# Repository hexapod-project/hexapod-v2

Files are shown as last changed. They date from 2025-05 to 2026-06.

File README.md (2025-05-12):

# Hexapod v2

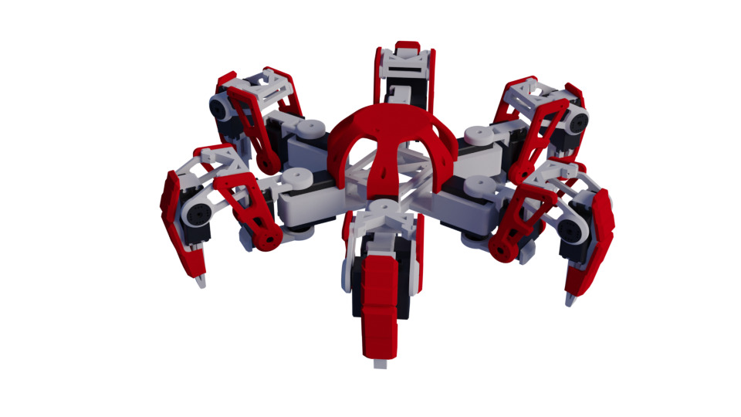
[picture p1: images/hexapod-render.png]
Hexapod v2


This is a hexapod robot that was built based on the previous version [(Hexapod v1)](https://github.com/hexapod-project/hexapod-v1) but with simpler basic features, more efficient inverse kinematics algorithm, and better structured code. This is a base that will be used for more advanced features in the future.

## Hardwares
- Microcontroller: Esp32
- Servo controller: PCA9685 (2 boards, 3 legs (9 servos) per board)
- Servos: 18 x DSPower Servo - S020A (30KG servo) (Or any other servos that has the same dimension, mounting points and max. torque)
- Batteries: 1 x 6v 2400mAh Ni-MH (for powering the microcontroller), 1 x 7.4v 2600mAh Li-ion/Ni-Mh (for powering the servos)
- Esp32 Expansion Shield (Optional)
- A switch (Optional) - Eg. Rocker switch or toggle switch

## Libraries

- Arduino Esp32
- Adafruit_PWMServoDriver
- PlatformIO

## Circuit Diagram

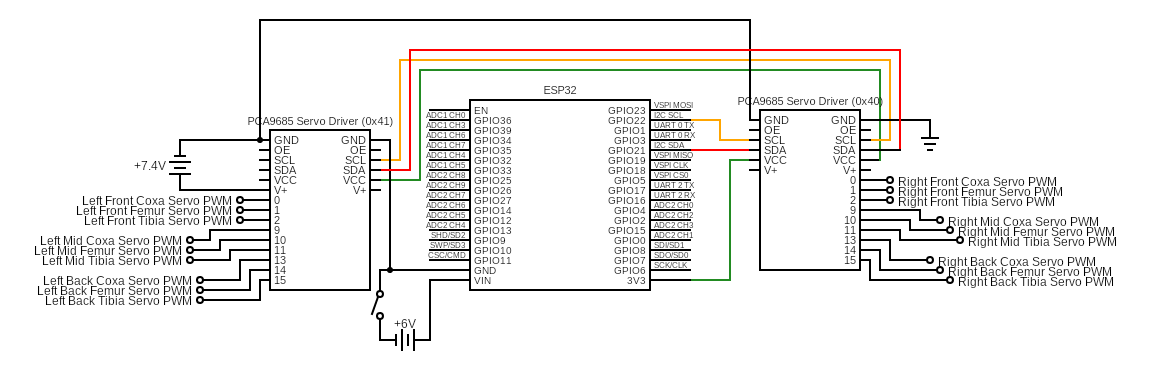
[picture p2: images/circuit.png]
Circuit Diagram


## Assembly

- All parts can be found in the [stl](/stl) folder
- The parts can be 3D printed using PLA with 0.4 nozzle.

##### Body

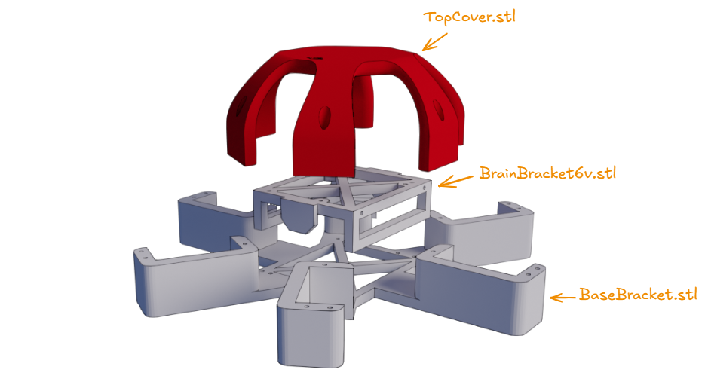
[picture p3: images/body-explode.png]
Body Explode View


- Use M3 x 20cm screws to attach the [TopCover.stl](/stl/TopCover.stl) to the [BaseBracket.stl](/stl/BaseBracket.stl)
- Use M3 screws to attach the ESP32 and PCA9685 Servo Drivers to the [BaseBracket.stl](/stl/BaseBracket.stl)

#### Servo

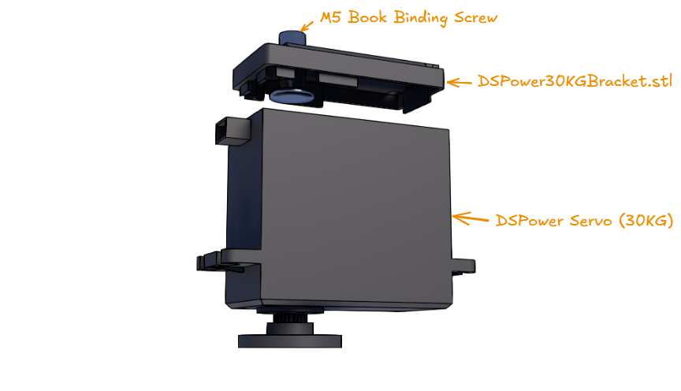
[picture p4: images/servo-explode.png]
Servo Explode View


- Remove the bottom cover of the servo and replace it with the [DSPower30KGBracket.stl](/stl/DSPower30KGBracket.stl) and insert a M5 Book Binding Screw to the hole as a pivot for the joints.

#### Leg

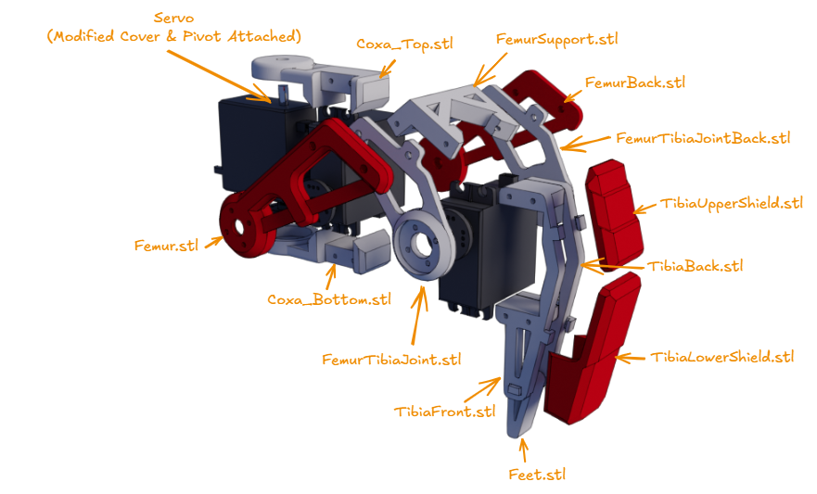
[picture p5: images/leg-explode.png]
Leg Explode View


- Assemble the leg parts according to the figure above.
- Use the screws provided by the servos to attach the parts to the servo.
- The legs are designed for the right legs but the parts can be flipped to be used for the left legs.

#### Body and Leg Attachment

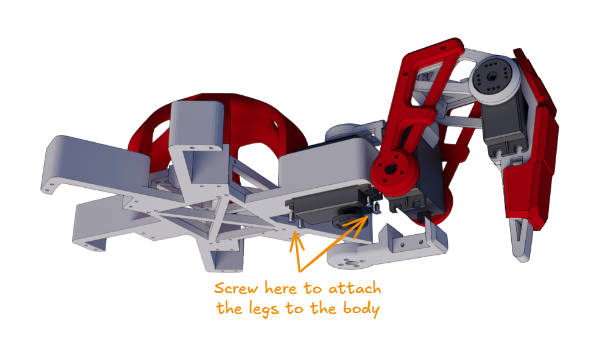
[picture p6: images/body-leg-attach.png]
Body and Leg Attachment


- Remove the CoxaBottom part and attach the leg to the body using the screws provided by the servos.

#### Final Assembly

Final Assembly

## Future Improvements

- Add Inertial Measurement Unit (IMU) for balancing
- Add LIDAR for obstacle detection
- Add GPS for position tracking
- Add path finding algorithm
- Migrate to Raspberry Pi for more processing power

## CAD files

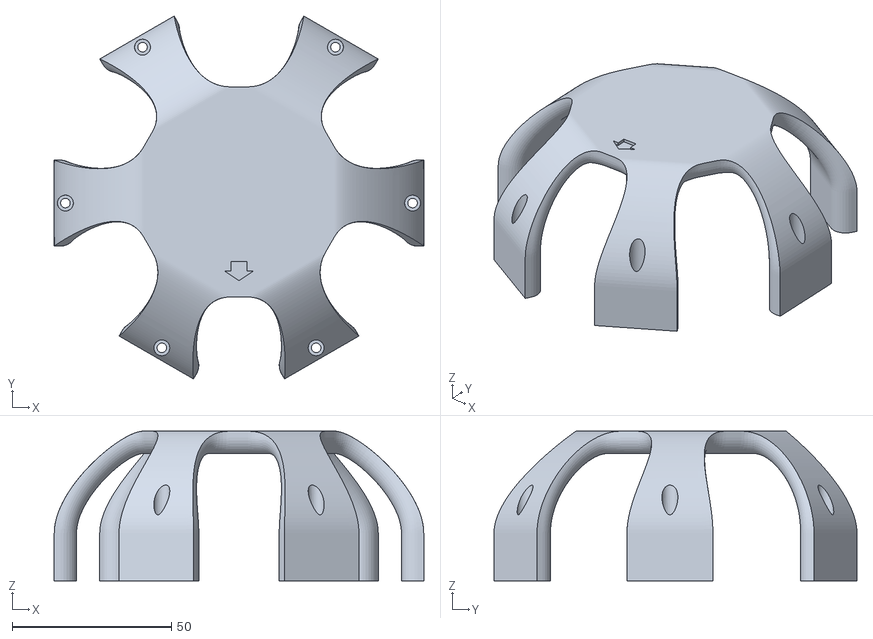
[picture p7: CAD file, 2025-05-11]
stl/TopCover.stl
116.0 x 114.0 x 47.0

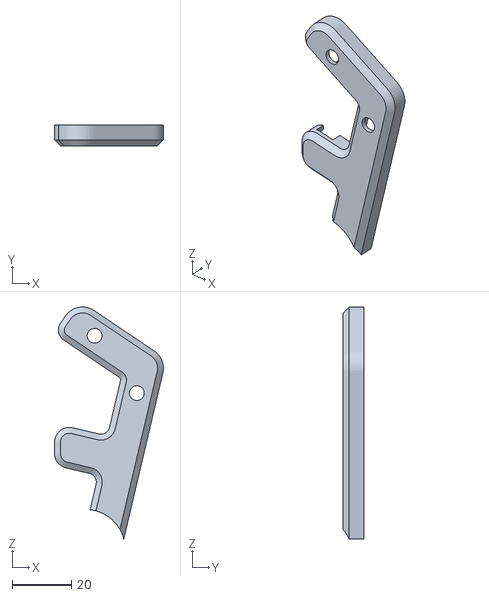
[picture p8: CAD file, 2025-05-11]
stl/FemurShield.stl
36.8 x 7.00 x 78.4

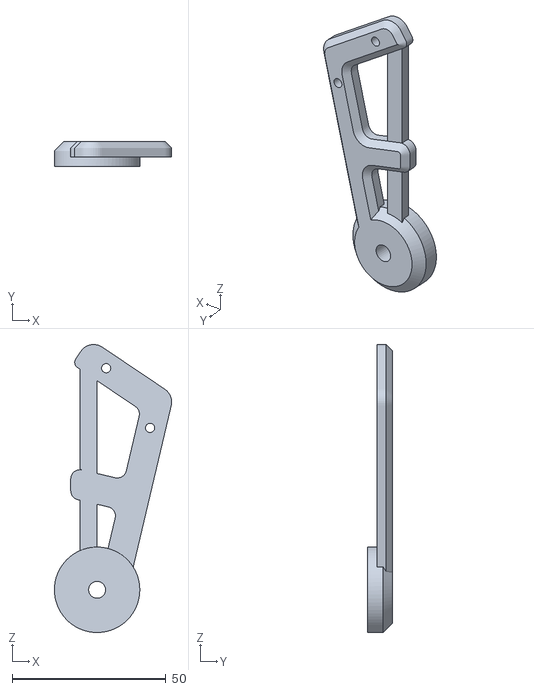
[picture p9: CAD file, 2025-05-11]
stl/FemurBack.stl
38.1 x 8.00 x 93.6

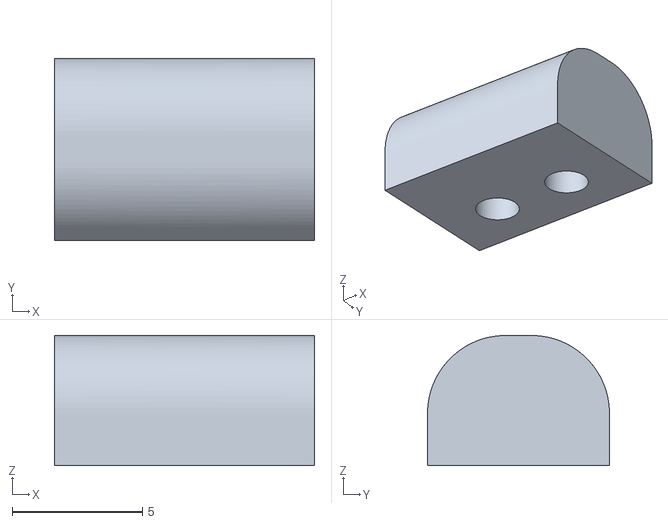
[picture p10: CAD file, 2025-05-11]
stl/BaterryBracke7.4v_Notch.stl
10.0 x 7.00 x 5.00

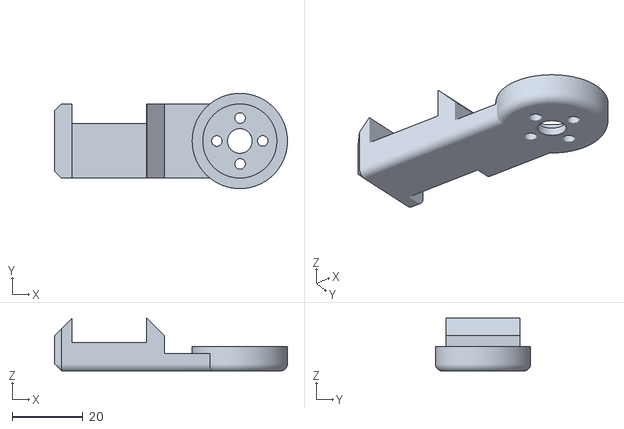
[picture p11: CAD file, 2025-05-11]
stl/Coxa_Bottom.stl
66.0 x 27.0 x 15.0

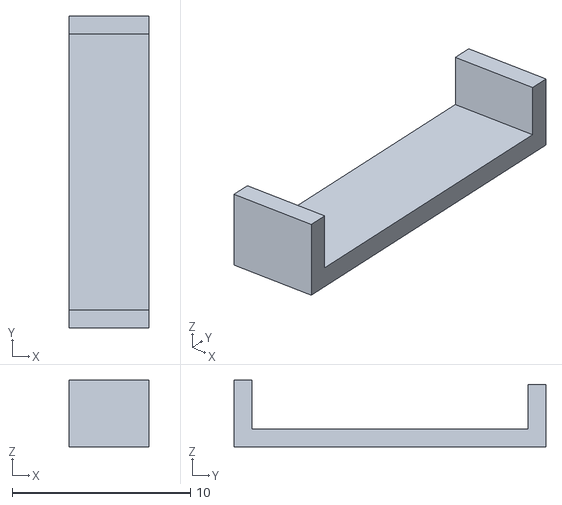
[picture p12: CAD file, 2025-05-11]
stl/DowelHolder.stl
4.50 x 17.5 x 3.75

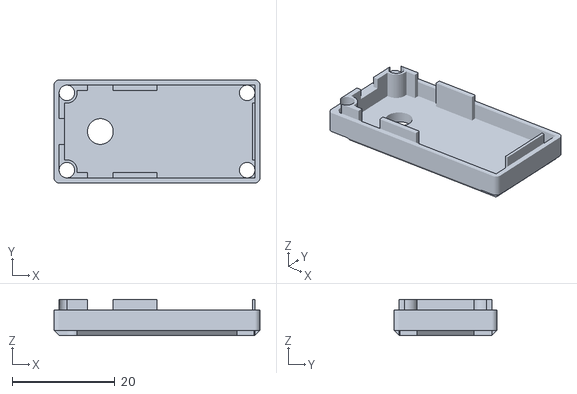
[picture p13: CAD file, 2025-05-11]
stl/DSPower30KGBracket.stl
40.0 x 20.0 x 7.00

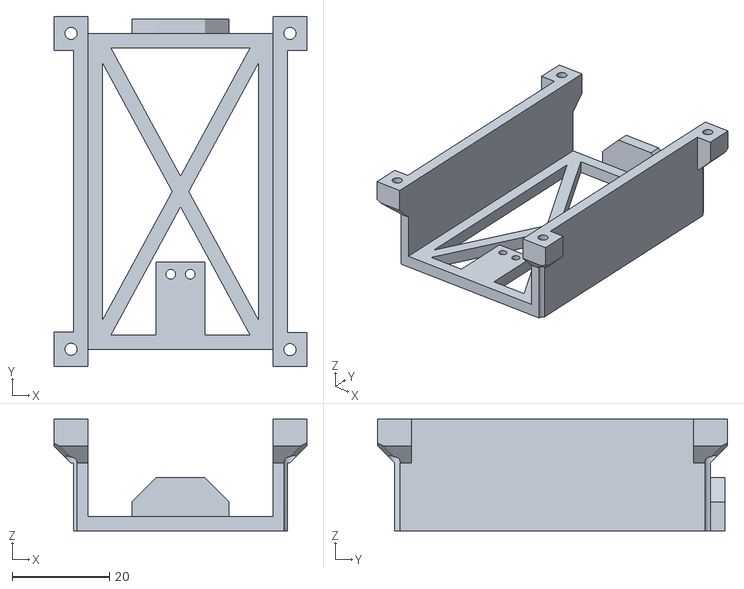
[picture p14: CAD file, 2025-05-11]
stl/BaterryBracke7.4v.stl
52.0 x 72.0 x 23.0

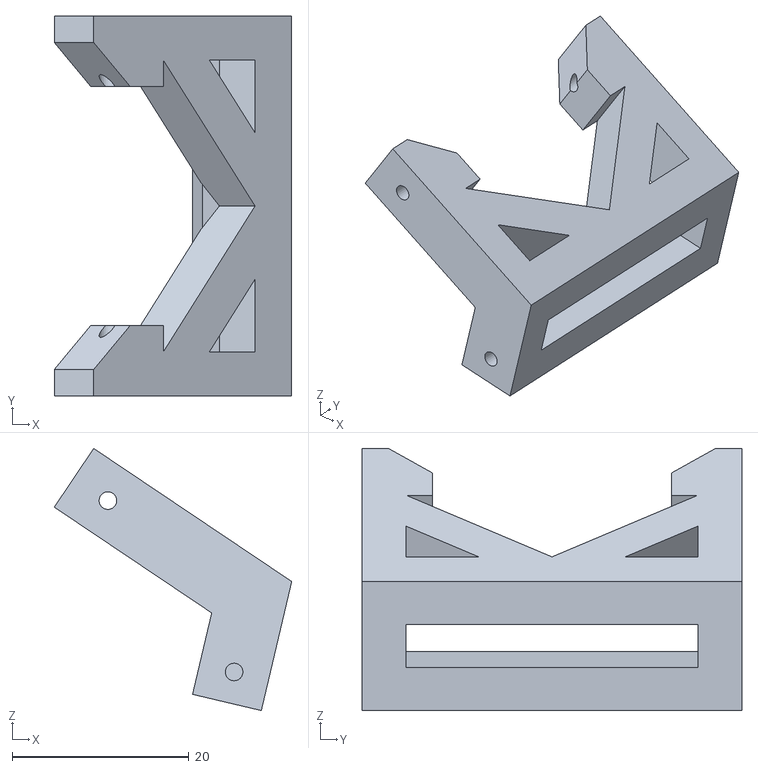
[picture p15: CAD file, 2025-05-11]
stl/FemurSupport.stl
26.9 x 43.0 x 29.7

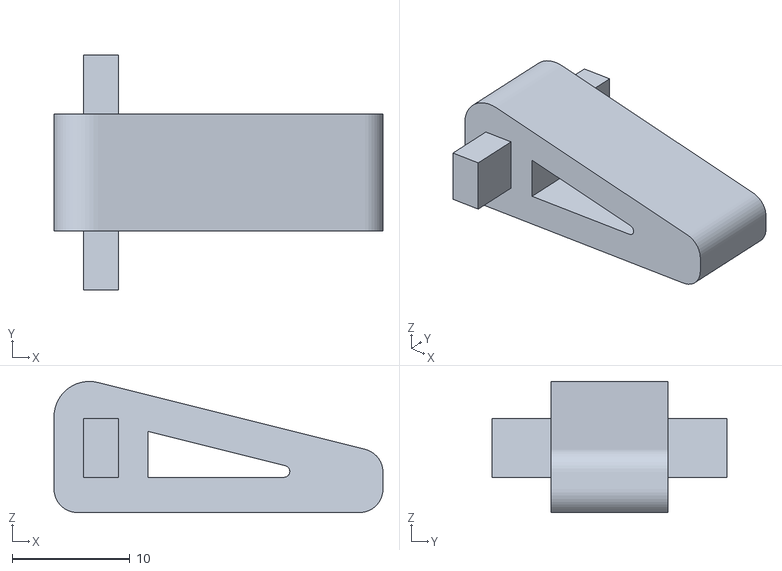
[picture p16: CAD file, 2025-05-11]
stl/Feet.stl
28.0 x 20.0 x 11.2

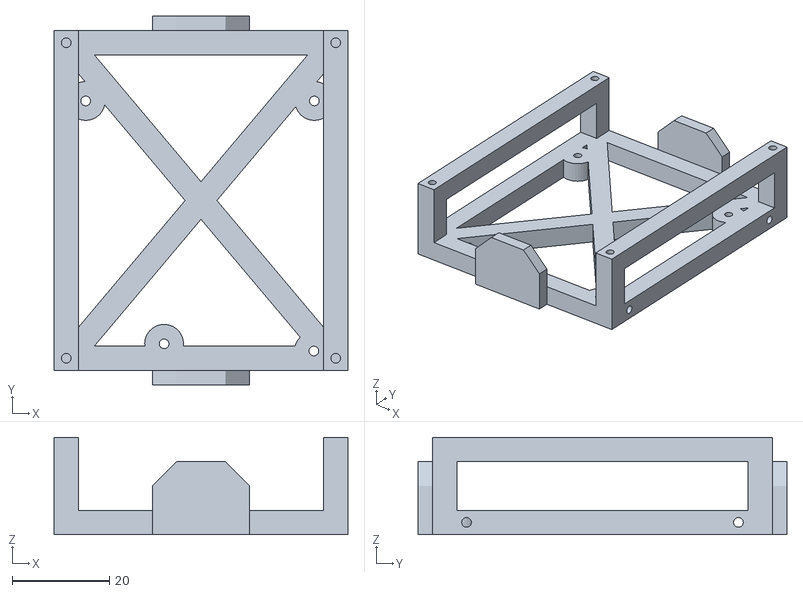
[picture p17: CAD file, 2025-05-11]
stl/BrainBracket6v.stl
60.5 x 76.0 x 20.0

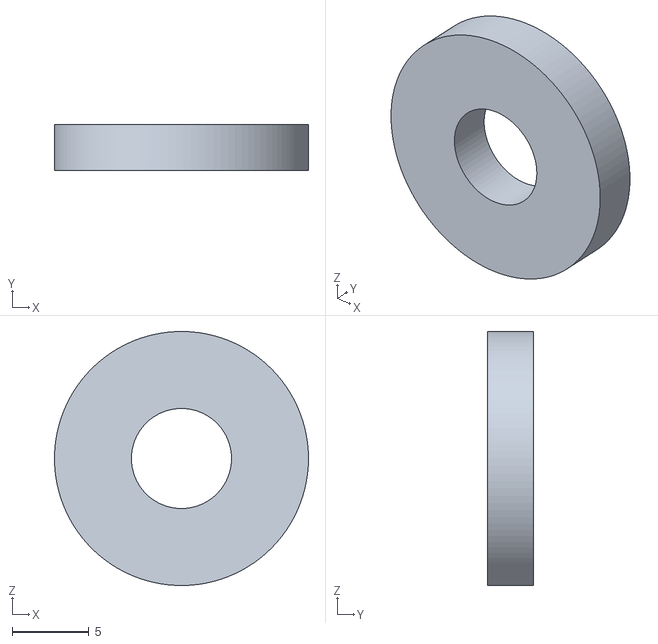
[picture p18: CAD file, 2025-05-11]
stl/Spacer_3mm.stl
16.5 x 3.00 x 16.5

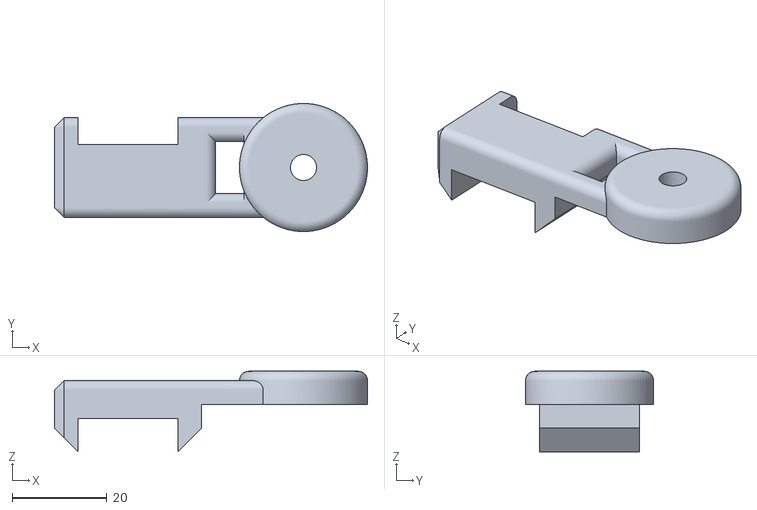
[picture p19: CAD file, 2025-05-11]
stl/Coxa_Top.stl
66.0 x 27.0 x 17.0

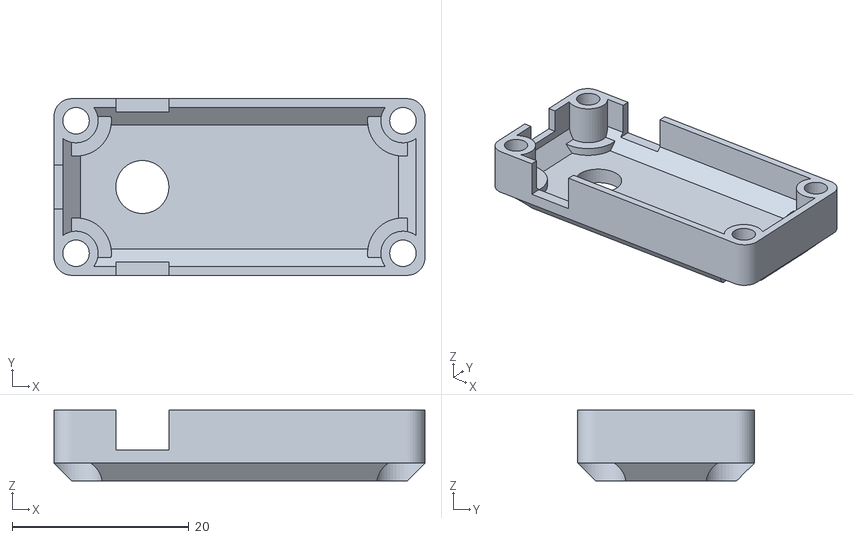
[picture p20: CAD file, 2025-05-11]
stl/ServoBracket.stl
42.0 x 20.0 x 8.00

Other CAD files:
stl/TibiaFront.stl
stl/Spacer_1mm.stl
stl/TibiaUpperShield.stl
stl/MagnetBracket_Male.stl
stl/BaseBracket.stl
stl/BaterryBracket7.4v_Notch2.stl
stl/BatteryBracket.stl
stl/BatteryBracket7.4v.stl
stl/BrainBracket.stl
stl/Femur.stl
stl/FemurTibiaJoint.stl
stl/FemurTibiaJointBack.stl
stl/MagnetBracket_Female.stl
stl/ServoBracket-DowelHolder.stl
stl/SwitchHolder.stl
stl/TibiaBack.stl
stl/TibiaLowerShield.stl
stl/Washer_2mmHole.stl

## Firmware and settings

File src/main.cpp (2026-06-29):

#include <string>
#include <Arduino.h>
#include <Preferences.h>

#include "Hexapod.h"
#include "Configuration.h"
#include "HexapodBLE.h"
#include "Constants.h"
#include "Calibrator.h"
#include "Utils.h"
#include "DisplayManager.h"
#include "MenuController.h"
#include "StateMachine.h"

bool isConnected = false;

int bluetoothMessage;
DisplayManager displayManager = DisplayManager();
Hexapod hexapod = Hexapod();
HexapodBLE hexapodBLE = HexapodBLE();
Calibrator calibrator = Calibrator(&hexapod);
StateMachine stateMachine = StateMachine();
MenuController menuController = MenuController(&displayManager, &calibrator, &stateMachine);

class HexapodBLEServerCallbacks : public BLEServerCallbacks
{
  void onConnect(BLEServer *server)
  {
    Serial.println("Bluetooh Connected");
    server->getAdvertising()->stop();
  }

  void onDisconnect(BLEServer *server)
  {
    Serial.println("Bluetooth Disconnected");
    server->startAdvertising();
    hexapod.stop();
  }
};

class MoveCharacteristicCallbacks : public BLECharacteristicCallbacks
{
  void onWrite(BLECharacteristic *characteristic)
  {
    std::string moveData = characteristic->getValue();
    int walkDirection = std::stoi(moveData);

    Serial.println(walkDirection);

    if (walkDirection >= 0)
    {
      hexapod.startWalk(walkDirection);
      stateMachine.moving(walkDirection);
    }
    else
    {
      hexapod.stop();
      stateMachine.idle();
    }
  }
};

class RotateCharacteristicCallbacks : public BLECharacteristicCallbacks
{
  void onWrite(BLECharacteristic *characteristic)
  {
    std::string moveData = characteristic->getValue();
    RotateDirection rotateDirection = static_cast<RotateDirection>(std::stoi(moveData));

    switch (rotateDirection)
    {
    case RotateDirection::ROTATE_LEFT:
    case RotateDirection::ROTATE_RIGHT:
      hexapod.startRotate(rotateDirection);
      break;
    default:
      hexapod.stop();
    }
  }
};

class RollPitchCharacteristicCallbacks : public BLECharacteristicCallbacks
{
  void onWrite(BLECharacteristic *characteristic)
  {
    std::string rollPitchData = characteristic->getValue();
    int rollPitchAngle = std::stoi(rollPitchData);

    if (rollPitchAngle >= 0)
    {
      hexapod.rollAndPitch(rollPitchAngle);
      if (rollPitchAngle >= 80 && rollPitchAngle <= 100)
      {
        // displayManager.displayAngryAnim();
      }
      else if (rollPitchAngle >= 260 && rollPitchAngle < 280)
      {
        // displayManager.displayHappyAnim();
      }
    }
    else
    {
      hexapod.stand();
    }
  }
};

class PWMPulseCharacteristicCallbacks : public BLECharacteristicCallbacks
{
  void onRead(BLECharacteristic *characteristic)
  {
    uint8_t *calibrationSettings = calibrator.getCalibrationSettings();
    std::string value = byteArrayToString(calibrationSettings, SERVO_COUNT * sizeof(u_int16_t));

    characteristic->setValue(value);
  }

  void onWrite(BLECharacteristic *characteristic)
  {
    std::string pwmPulseData = characteristic->getValue();

    uint8_t servoIndex = pwmPulseData[0];
    uint16_t pulse = (pwmPulseData[1] << 8) | pwmPulseData[2];

    calibrator.setPWMPulse(servoIndex, pulse);
  }
};

class MoveServoCharacteristicCallbacks : public BLECharacteristicCallbacks
{
  void onWrite(BLECharacteristic *characteristic)
  {
    std::string pwmPulseData = characteristic->getValue();

    uint8_t servoIndex = pwmPulseData[0];
    short angle = pwmPulseData[1] + SERVO_ANGLES_MIN;

    calibrator.testServoAngle(servoIndex, angle);
  }
};

class HexapodModeCharacteristicCallbacks : public BLECharacteristicCallbacks
{
  void onRead(BLECharacteristic *characteristic)
  {
    HexapodMode mode = hexapod.getMode();

    characteristic->setValue(std::to_string(mode));
  }

  void onWrite(BLECharacteristic *characteristic)
  {
    std::string modeData = characteristic->getValue();
    HexapodMode mode = static_cast<HexapodMode>(std::stoi(modeData));

    hexapod.switchMode(mode);
  }
};

class HexapodRestCharacteristicCallbacks : public BLECharacteristicCallbacks
{
  void onRead(BLECharacteristic *characteristic)
  {
    bool isSleep = stateMachine.getState() == STATE_SLEEP;

    characteristic->setValue(std::to_string(isSleep));
  }

  void onWrite(BLECharacteristic *characteristic)
  {
    std::string isSleep = characteristic->getValue();

    if (isSleep == "1")
    {
      stateMachine.sleep();
    }
    else
    {
      stateMachine.idle();
    }
  }
};

void setup()
{
  Serial.begin(115200);

  hexapodBLE.initBLE(new HexapodBLEServerCallbacks(),
                     new MoveCharacteristicCallbacks(),
                     new RotateCharacteristicCallbacks(),
                     new RollPitchCharacteristicCallbacks(),
                     new PWMPulseCharacteristicCallbacks(),
                     new MoveServoCharacteristicCallbacks(),
                     new HexapodModeCharacteristicCallbacks(),
                     new HexapodRestCharacteristicCallbacks());

  calibrator.init();
  displayManager.init();
  displayManager.startLoading();

  hexapod.init();

  displayManager.stopLoading();
  menuController.init();

  stateMachine.init();
  stateMachine.idle();
}

void loop()
{
  menuController.loop();
  displayManager.loop();
  stateMachine.loop();
}

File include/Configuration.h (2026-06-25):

#pragma once

#include <map>
#include "Servo.h"
#include "Leg.h"
#include "Vec3.h"
#include <Adafruit_PWMServoDriver.h>

// 0 = Hexapod, 1 = Servo Calibration, 2 = Servo Tests
#define MODE 0
#define DEBUG_MODE_LEGS false
#define SERIAL_CONTROL_MODE false

// Servo Constants
#define SERVO_ANGLES_MIN -75
#define SERVO_ANGLES_MAX 75
#define PWM_FREQ 60

#define SCREEN_WIDTH 128  // OLED display width, in pixels
#define SCREEN_HEIGHT 64  // OLED display height, in pixels
#define HALF_SCREEN_WIDTH SCREEN_WIDTH/2
#define HALF_SCREEN_HEIGHT SCREEN_HEIGHT/2
#define OLED_RESET -1    // Reset pin # (or -1 if sharing Arduino reset pin)
#define OLED_I2C_ADDRESS 0x3C

extern Adafruit_PWMServoDriver *servoDriverRight;
extern Adafruit_PWMServoDriver *servoDriverLeft;

extern std::map<int, Servo *> SERVOS;

// Leg Constants
// Lengths in mm
#define COXA_DISTANCE_FROM_CENTER 90
#define FEMUR_TO_COXA_DISTANCE 40
#define FEMUR_LENGTH 70
#define TIBIA_LENGTH 90

extern std::map<int, Leg *> LEGS;

// Body Positions
#define BODY_OFFSET_Z 10

// Feet Properties
#define REST_HEIGHT 0
#define STAND_HEIGHT 50
#define FEET_DISTANCE_FROM_CENTER_REST 180
#define FEET_DISTANCE_FROM_CENTER_STANDING 190

extern std::map<int, Vec3 *> FEET_POSITIONS_STANDING;
extern std::map<int, Vec3 *> FEET_POSITIONS_REST;

// Step Properties
#define STEP_FRAMERATE 24 // How often to update the gaits
#define STEP_DISTANCE 150
#define STEP_HEIGHT 80
#define STEP_DURATION 0.3 // in seconds +500ms(i2c delay)

// Roll Pitch Properties
#define ROLL_ANGLE 20
#define PITCH_ANGLE 20

// Rotate Properties
#define ROTATE_ANGLE_PER_STEP 20

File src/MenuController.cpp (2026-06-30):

#include "MenuController.h"
#include "Constants.h"
#include <Arduino.h>

std::map<MenuScreen, String> MENU_LABELS = {
    {MENU_MAIN, "Main Menu"},
    {MENU_MOOD, "Change Mood"},
    {MENU_CALIBRATE, "Calibrate"},
    {MENU_SLEEP, "Sleep"},
    {MENU_OFF, "Power Off"},
    {MENU_RESET, "Reset to Default"},
    {MENU_RESET_CONFIRMATION, "Reset to Default"},
    {MENU_EXIT, "Exit"},
    {MENU_BACK, "Back"},

    {MENU_MOOD_NEUTRAL, "Neutral"},
    {MENU_MOOD_HAPPY, "Happy"},
    {MENU_MOOD_SAD, "Sad"},
    {MENU_MOOD_ANGRY, "Angry"},
    {MENU_MOOD_TIRED, "Tired"},
    {MENU_MOOD_SLEEP, "Sleep"},

    {MENU_CALIBRATE_LF_COXA, "Left Front Coxa"},
    {MENU_CALIBRATE_LM_COXA, "Left Mid Coxa"},
    {MENU_CALIBRATE_LB_COXA, "Left Back Coxa"},
    {MENU_CALIBRATE_RF_COXA, "Right Front Coxa"},
    {MENU_CALIBRATE_RM_COXA, "Right Mid Coxa"},
    {MENU_CALIBRATE_RB_COXA, "Right Back Coxa"},

    {MENU_CALIBRATE_LF_FEMUR, "Left Front Femur"},
    {MENU_CALIBRATE_LM_FEMUR, "Left Mid Femur"},
    {MENU_CALIBRATE_LB_FEMUR, "Left Back Femur"},
    {MENU_CALIBRATE_RF_FEMUR, "Right Front Femur"},
    {MENU_CALIBRATE_RM_FEMUR, "Right Mid Femur"},
    {MENU_CALIBRATE_RB_FEMUR, "Right Back Femur"},

    {MENU_CALIBRATE_LF_TIBIA, "Left Front Tibia"},
    {MENU_CALIBRATE_LM_TIBIA, "Left Mid Tibia"},
    {MENU_CALIBRATE_LB_TIBIA, "Left Back Tibia"},
    {MENU_CALIBRATE_RF_TIBIA, "Right Front Tibia"},
    {MENU_CALIBRATE_RM_TIBIA, "Right Mid Tibia"},
    {MENU_CALIBRATE_RB_TIBIA, "Right Back Tibia"},
};

std::map<Joint, String> JOINT_LABELS = {
    {Joint::LEFT_FRONT_COXA, "Calibrate LF Coxa"},
    {Joint::LEFT_MID_COXA, "Calibrate LM Coxa"},
    {Joint::LEFT_BACK_COXA, "Calibrate LB Coxa"},
    {Joint::RIGHT_FRONT_COXA, "Calibrate RF Coxa"},
    {Joint::RIGHT_MID_COXA, "Calibrate RM Coxa"},
    {Joint::RIGHT_BACK_COXA, "Calibrate RB Coxa"},
    {Joint::LEFT_FRONT_FEMUR, "Calibrate LF Femur"},
    {Joint::LEFT_MID_FEMUR, "Calibrate LM Femur"},
    {Joint::LEFT_BACK_FEMUR, "Calibrate LB Femur"},
    {Joint::RIGHT_FRONT_FEMUR, "Calibrate RF Femur"},
    {Joint::RIGHT_MID_FEMUR, "Calibrate RM Femur"},
    {Joint::RIGHT_BACK_FEMUR, "Calibrate RB Femur"},
    {Joint::LEFT_FRONT_TIBIA, "Calibrate LF Tibia"},
    {Joint::LEFT_MID_TIBIA, "Calibrate LM Tibia"},
    {Joint::LEFT_BACK_TIBIA, "Calibrate LB Tibia"},
    {Joint::RIGHT_FRONT_TIBIA, "Calibrate RF Tibia"},
    {Joint::RIGHT_MID_TIBIA, "Calibrate RM Tibia"},
    {Joint::RIGHT_BACK_TIBIA, "Calibrate RB Tibia"},
};

const Joint CALIBRATE_JOINT_ORDERS[] = {
    Joint::RIGHT_FRONT_COXA,
    Joint::RIGHT_FRONT_FEMUR,
    Joint::RIGHT_FRONT_TIBIA,
    Joint::RIGHT_MID_COXA,
    Joint::RIGHT_MID_FEMUR,
    Joint::RIGHT_MID_TIBIA,
    Joint::RIGHT_BACK_COXA,
    Joint::RIGHT_BACK_FEMUR,
    Joint::RIGHT_BACK_TIBIA,
    Joint::LEFT_BACK_TIBIA,
    Joint::LEFT_BACK_FEMUR,
    Joint::LEFT_BACK_COXA,
    Joint::LEFT_MID_TIBIA,
    Joint::LEFT_MID_FEMUR,
    Joint::LEFT_MID_COXA,
    Joint::LEFT_FRONT_TIBIA,
    Joint::LEFT_FRONT_FEMUR,
    Joint::LEFT_FRONT_COXA,
};

void changeMood(FaceExpression expression)
{
    DisplayManager *displayManager = DisplayManager::getInstance();

    displayManager->changeMood(expression);
    displayManager->exitMenu();
}

void openCalibratorSelector(int jointIndex = 1)
{
    if (jointIndex > sizeof(CALIBRATE_JOINT_ORDERS) - 1)
    {
        jointIndex = 1;
    }

    MenuController *menuController = MenuController::getInstance();
    DisplayManager *displayManager = DisplayManager::getInstance();

    menuController->setScreen(MENU_CALIBRATE);
    menuController->setCursorValue(jointIndex);

    if (jointIndex > 0)
    {
        Joint joint = CALIBRATE_JOINT_ORDERS[jointIndex - 1];
        displayManager->showCalibratorSelector(JOINT_LABELS[joint], joint);
    }
}

void openCalibratorSetter(MenuScreen screen, Joint joint)
{
    MenuController *menuController = MenuController::getInstance();
    DisplayManager *displayManager = DisplayManager::getInstance();
    Calibrator *calibrator = Calibrator::getInstance();
    Hexapod *hexapod = Hexapod::getInstance();

    hexapod->switchMode(HexapodMode::CALIBRATE);
    menuController->setScreen(screen);
    uint16_t pwm = calibrator->getPWMPulse(joint - 1);
    menuController->setSelectedJoint(joint);
    menuController->setCursorValue(pwm);
    displayManager->showCalibratorSetter(MENU_LABELS[screen], pwm);
}

void openResetToDefaultConfirmation()
{
    MenuController *menuController = MenuController::getInstance();
    DisplayManager *displayManager = DisplayManager::getInstance();

    menuController->setScreen(MENU_RESET_CONFIRMATION);
    menuController->setCursorValue(0);
    displayManager->showConfirmation(MENU_LABELS[MENU_RESET_CONFIRMATION], "Are you sure?", false);
}

void onResetToDefaultConfirmed()
{
    MenuController *menuController = MenuController::getInstance();
    menuController->resetToDefault();
}

void onSleep()
{
    StateMachine *stateMachine = StateMachine::getInstance();
    DisplayManager *displayManager = DisplayManager::getInstance();

    stateMachine->sleep();
    displayManager->exitMenu();
}

void onTurnOff()
{
    MenuController *menuController = MenuController::getInstance();
    menuController->turnOff();
}
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

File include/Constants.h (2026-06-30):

#pragma once

#include <BLECharacteristic.h>
#include <BLEUtils.h>
#include <string>

#define SERVO_COUNT 18

#define DATA_DELIMITER '|'

#define NAME "HEXBOTv2"
#define PRODUCT_CODE "01"

#define CONCAT(x, y) x##y
#define STR(x) #x
#define SKU NAME "-" PRODUCT_CODE

#define HEXAPOD_SERVICE_UUID "a9b02c9e-1b0b-4b97-8b68-80af4a3bc6c4"
extern BLECharacteristic HEXAPOD_MODE_CHARACTERISTIC;
extern BLECharacteristic HEXAPOD_REST_CHARACTERISTIC;

// Motion service
#define MOTION_SERVICE_UUID "42e91a79-610e-40b3-8873-fd65d2c0d581"
extern BLECharacteristic MOVE_CHARACTERISTIC;
extern BLECharacteristic ROTATE_CHARACTERISTIC;
extern BLECharacteristic ROLLPITCH_CHARACTERISTIC;

// Calibrate service
#define CALIBRATE_SERVICE_UUID "2f35a75b-1a6c-481d-b781-22f5d3c17420"
extern BLECharacteristic PWM_PULSE_CHARACTERISTIC;
extern BLECharacteristic MOVE_SERVO_CHARACTERISTIC;

#define SERVO_PULSE_INTERVAL 750

#define MIN_PWM 500
#define MAX_PWM 2500
#define AVG_PWM (MAX_PWM - MIN_PWM) / 2 + MIN_PWM

#define CLK_PIN 25 // ESP32 pin GPIO25 connected to the rotary encoder's CLK pin
#define DT_PIN 26  // ESP32 pin GPIO26 connected to the rotary encoder's DT pin
#define SW_PIN 27  // ESP32 pin GPIO27 connected to the rotary encoder's SW pin

#define SLEEP_DELAY 5000

#define STATE_DURATION_IDLE_TO_SLEEP 300000
#define STATE_DURATION_SLEEP_TO_OFF 120000

#define MAX_EYE_X_OFFSET HALF_SCREEN_WIDTH - EYE_WIDTH - EYE_GAP/2

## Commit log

2024-02-29 Added base inverse kinematics and calibrated servos
    [Configuration.h, configuration.h]
2024-03-03 Added walk and rotate motion
    [Configuration.h]
2024-04-07 Added bluetooth connectivity for mobile controller
    [Configuration.h]
2024-04-09 Update configurations for new servos
    [Configuration.h]
2024-04-10 Added roll pitch and rest stance
    [Configuration.h]
2025-05-11 Add STL files
    [BaseBracket.stl, BaterryBracke7.4v.stl, BaterryBracke7.4v_Notch.stl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]
2026-06-20 Added OLED screen support and face animations
    [Configuration.h]
2026-06-23 Added settings menu
    [Configuration.h]
2026-06-25 Added calibration setter
    [Configuration.h]
2026-06-25 Added calibrator UI
2026-06-26 Added "Power Off" option
2026-06-30 Fixed calibrator selections issues and added reset to default option
    [Calibrator.cpp, Constants.h, DisplayManager.cpp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]
